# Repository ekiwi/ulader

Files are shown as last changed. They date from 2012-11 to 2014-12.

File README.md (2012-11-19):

# uLader #

This project aims at creating a backup battery powered bike
lighting system.
It borrows from the great work done by the developers of the
Forumslader and acknowledges this by incorporation
Lader (german for charger) into its name.
The u stands for the micro controller used in this design,
the use of which is going to add a lot more flexibility.

## Component Overview ##

The uLader system consists of these components:
* Main Board: atmega88 uC, ac to dc circuit, charging circuit, 
control switches
* Tail Light: red low power led (dimmable), photo transistor
* Front Light: attiny uC, white low power DLR (dimmabel), white 3W led 
(dimmable), photo transistor
* 2x Rotation Sensor: front and back

## Optional/Future Features ##
* White LED(s) underneath the saddle that can be turned on to find your locks
keyhole
* Pressure Sensor underneath/in the saddle to detect if someone is riding the
bike
* Turn signals on front and back

### Main Board ###

The main board contains the circuit that converts the power from the bike
dynamo, which acts approximately like an AC current source, to about 12V DC.
This circuit is heavily based on the awesome work done by the people behind
the [Forumslader project](forumslader.de).
This circuit is also responsible for charging the LiFePo4 accumulators used.
Check out [forumnslader.de]
(http://www.forumslader.de/Akkus-fuer-12V-Lader.189.0.html) if you want to use
different batteries.

The micro controller part of the Main Board features an atmega88. It was choosen,
because of its ease of use, its low power consumption and because if the number
of pins available.
The atmega is used for the following:
* power mangagement
    * check charging status
    * (indicate status??)
    * cut of power to all devices when battery cells run low
* lighting control
    * measure light intensity
    * measure speed
    * control which lights need to be on and how bright they need to be
    * in auto mode decide when to turn on which lights and auto dim

### Tail Light ####

The Tail Light needs to ensure visibility during the night (and day) from the 
back as well as from the side. In addition to that it must not blind other 
people.  
The CAT4201 led step down driver is used in combination with an OSRAM Top LED
in order to provide a low power solution for these requirements. The tail
light also includes a photo transistor for measuring the ambient light.  
It should be tested if visibility from the side of your bike can be enhanced
by adding one LED on each side.

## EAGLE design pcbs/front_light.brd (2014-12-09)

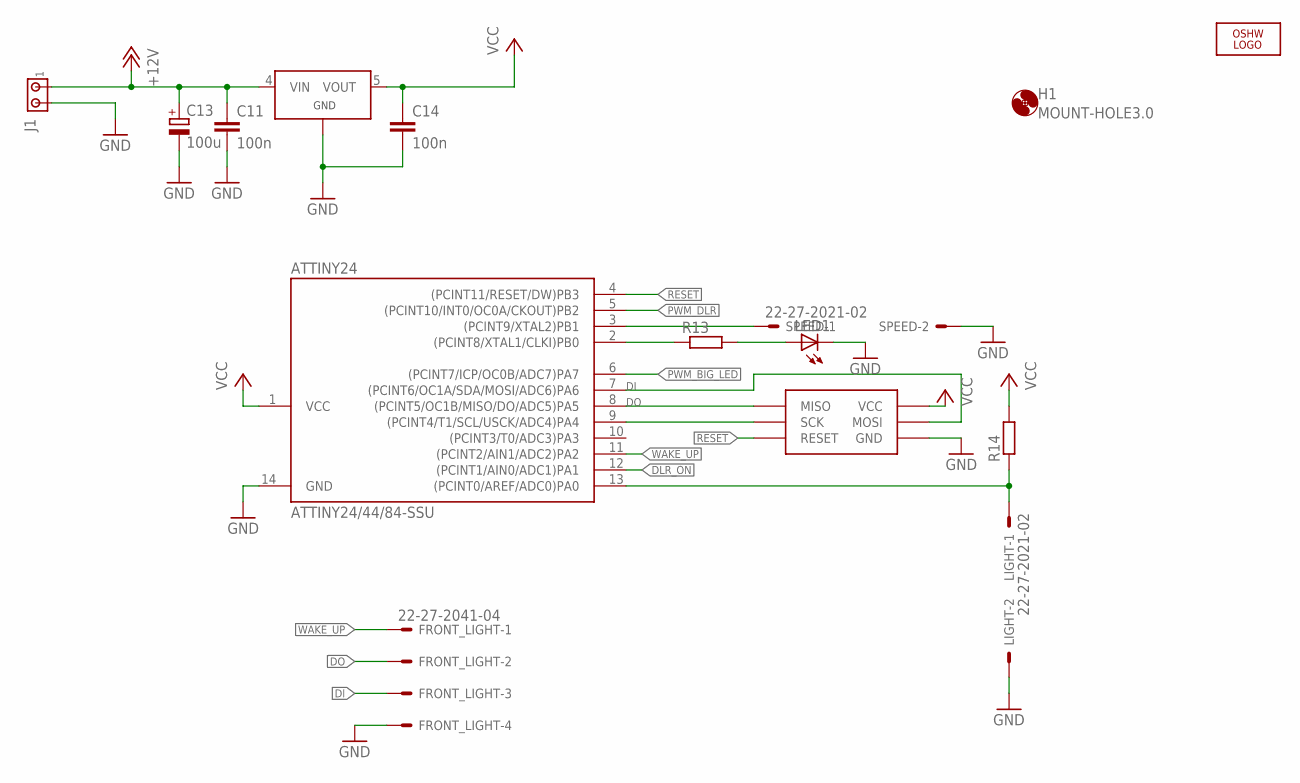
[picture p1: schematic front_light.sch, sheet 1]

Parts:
ATTINY24: ATTINY24/44/84-SSU; SOIC14
C11, C14: 100n; C0603
C13: 100u; PANASONIC_E
FRONT_LIGHT: 22-27-2041-04; 6410-04
H1: MOUNT-HOLE3.0; 3,0
J1: MTA02-156; 1X2MTA
LED1: LEDCHIPLED_0603; CHIPLED_0603
LIGHT: 22-27-2021-02; 6410-02
LOGO2: OSHW_LOGO_6MILX0150-NT; OSHW_6X150_NOTEXT
R13, R14: R-EU_R0603; R0603
SPEED: 22-27-2021-02; 6410-02
U$1: TPS71530; SOT23-DBV
U$2: ISP_SPECIALS; ISP_RM2_00_STRAIGHT

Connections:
+12V: C11.1, C13.+, J1.1, U$1.4 (VIN); also elsewhere on the board
DI: ATTINY24.7 ((PCINT6/OC1A/SDA/MOSI/ADC6)PA6), FRONT_LIGHT.3, U$2.MOSI
DLR_ON: ATTINY24.12 ((PCINT1/AIN0/ADC1)PA1); also elsewhere on the board
DO: ATTINY24.8 ((PCINT5/OC1B/MISO/DO/ADC5)PA5), FRONT_LIGHT.2, U$2.RESET (MISO)
GND: ATTINY24.14 (GND), C11.2, C13.-, C14.2, FRONT_LIGHT.4, J1.2, LED1.C, LIGHT.2, SPEED.2, U$1.2 (GND), U$2.VCC (GND); also elsewhere on the board
unnamed: ATTINY24.3 ((PCINT9/XTAL2)PB1), SPEED.1
unnamed: ATTINY24.9 ((PCINT4/T1/SCL/USCK/ADC4)PA4), U$2.SCK
unnamed: ATTINY24.13 ((PCINT0/AREF/ADC0)PA0), LIGHT.1, R14.1
unnamed: ATTINY24.2 ((PCINT8/XTAL1/CLKI)PB0), R13.1
unnamed: LED1.A, R13.2
PWM_BIG_LED: ATTINY24.6 ((PCINT7/ICP/OC0B/ADC7)PA7); also elsewhere on the board
PWM_DLR: ATTINY24.5 ((PCINT10/INT0/OC0A/CKOUT)PB2); also elsewhere on the board
RESET: ATTINY24.4 ((PCINT11/RESET/DW)PB3), U$2.MISO (RESET)
VCC: ATTINY24.1 (VCC), C14.1, R14.2, U$1.5 (VOUT), U$2.GND (VCC)
WAKE_UP: ATTINY24.11 ((PCINT2/AIN1/ADC2)PA2), FRONT_LIGHT.1

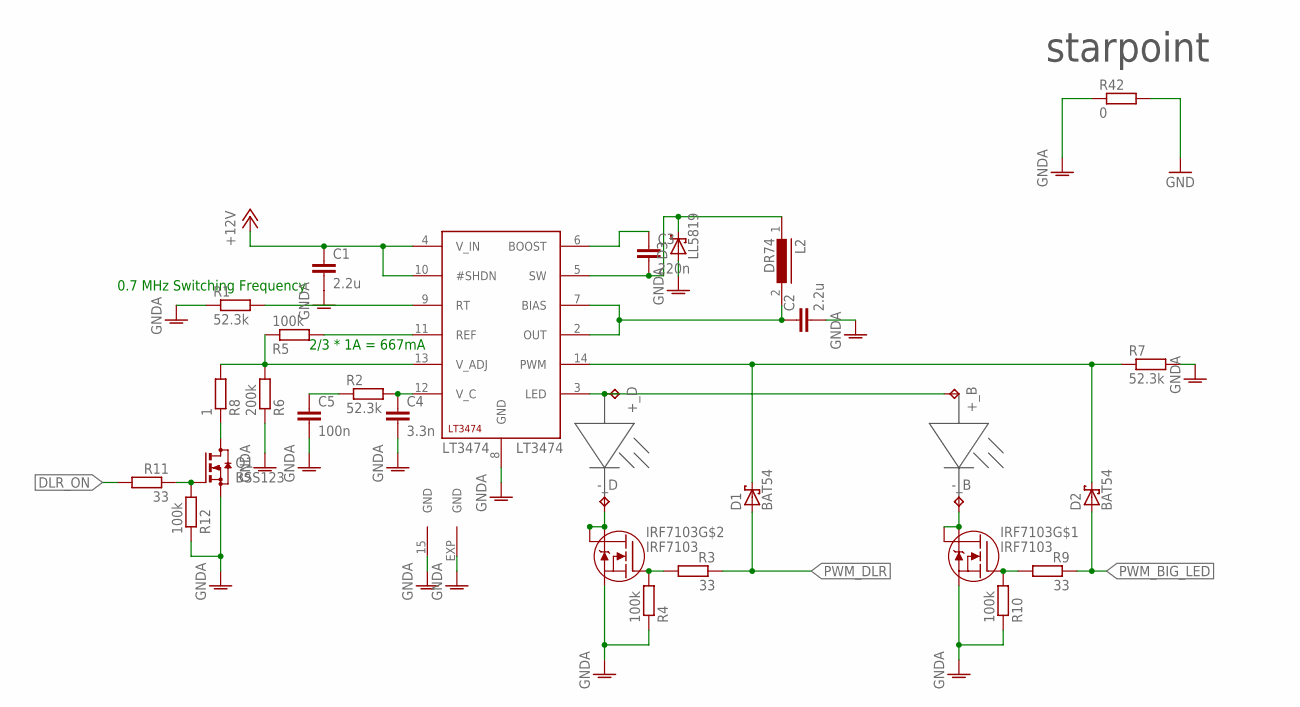
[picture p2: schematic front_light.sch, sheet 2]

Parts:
+_B: TPTP20SQ; TP20SQ
+_D: TPTP20SQ; TP20SQ
-_B: TPTP20SQ; TP20SQ
-_D: TPTP20SQ; TP20SQ
C1, C2: 2.2u; C0805
C3: 220n; C0603
C4: 3.3n; C0603
C5: 100n; C0603
D1, D2: BAT54; SOT23
D3: LL5819; MELF-MLL41
IRF7103: IRF7103; SO8-2
L2: DR74
LT3474: LT3474; TSSOP16_BA
Q1: BSS123; SOT23
R1, R2, R7: 52.3k; R0603
R3, R9, R11: 33; R0603
R4, R5, R10, R12: 100k; R0603
R6: 200k; R0603
R8: 1; R0603
R42: 0; R0603

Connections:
+12V: C1.1, LT3474.4 (V_IN), LT3474.10 (#SHDN); also elsewhere on the board
DLR_ON: R11.2; also elsewhere on the board
GND: R42.2; also elsewhere on the board
GNDA: C1.2, C2.2, C4.2, C5.2, D3.A, IRF7103.1 (S), IRF7103.3 (S), LT3474.8 (GND), LT3474.15 (GND), LT3474.EXP (GND), Q1.2 (S), R1.1, R4.1, R6.1, R7.2, R10.1, R12.1, R42.1
unnamed: C3.2, D3.C, L2.1, LT3474.5 (SW)
unnamed: C2.1, L2.2, LT3474.2 (OUT), LT3474.7 (BIAS)
unnamed: LT3474.11 (REF), R5.2
unnamed: LT3474.9 (RT), R1.2
unnamed: C3.1, LT3474.6 (BOOST)
unnamed: C4.1, LT3474.12 (V_C), R2.2
unnamed: C5.1, R2.1
unnamed: +_B.TP, +_D.TP, LT3474.3 (LED)
unnamed: -_D.TP, IRF7103.5 (D), IRF7103.6 (D)
unnamed: IRF7103.4 (G), R3.2, R4.2
unnamed: LT3474.13 (V_ADJ), R5.1, R6.2, R8.2
unnamed: Q1.3 (D), R8.1
unnamed: Q1.1 (G), R11.1, R12.2
unnamed: -_B.TP, IRF7103.7 (D), IRF7103.8 (D)
unnamed: IRF7103.2 (G), R9.2, R10.2
PWM: D1.3 (C), D2.3 (C), LT3474.14 (PWM), R7.1
PWM_BIG_LED: D2.1 (A), R9.1; also elsewhere on the board
PWM_DLR: D1.1 (A), R3.1; also elsewhere on the board

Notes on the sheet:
0.7 MHz Switching Frequency
2/3 * 1A = 667mA
starpoint

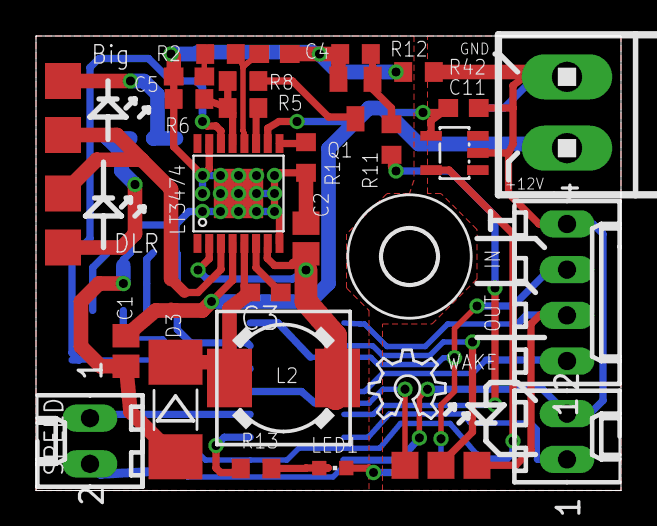
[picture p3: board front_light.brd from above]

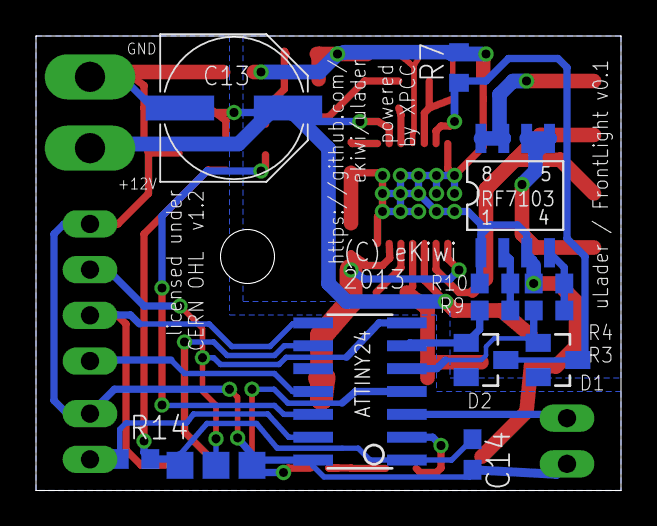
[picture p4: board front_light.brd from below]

Board: 2 copper layers, 32.5 x 25.2 mm, 44 parts (12 on the bottom side), 32 nets.

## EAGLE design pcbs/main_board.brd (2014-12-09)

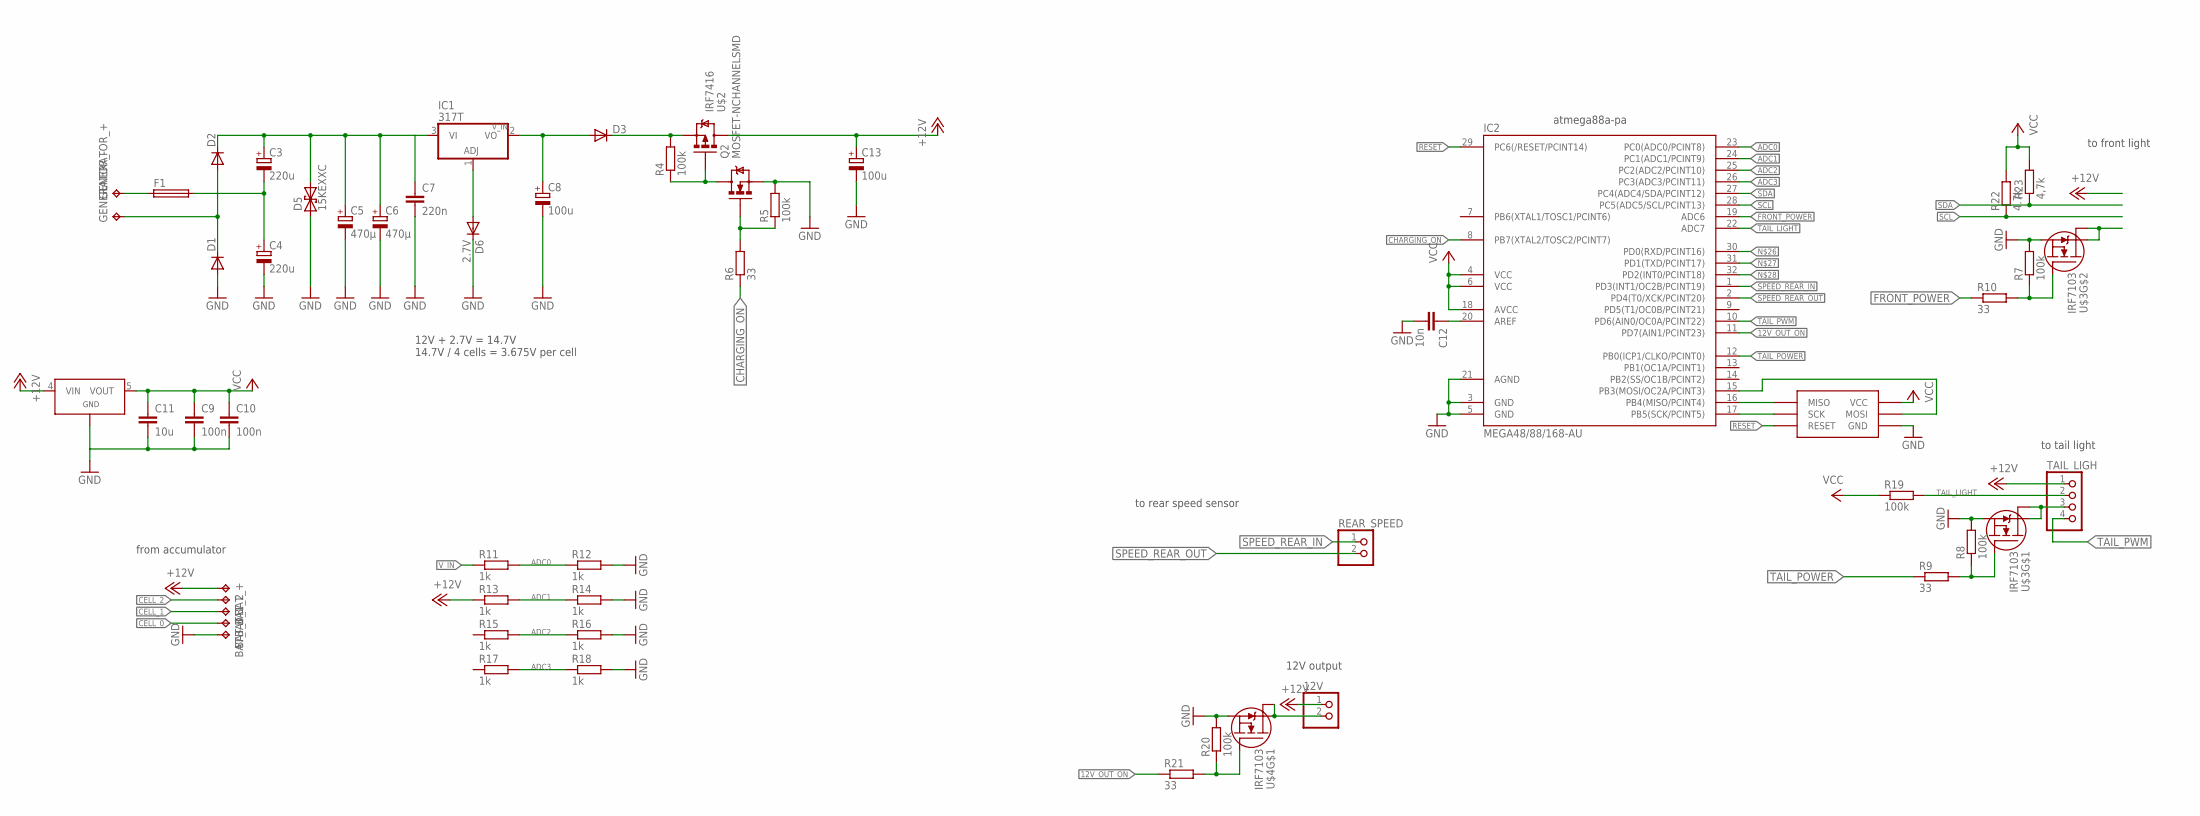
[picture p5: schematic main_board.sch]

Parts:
12V: PINHD-1X2; 1X02
BAT_0, BAT_1, BAT_2: TPTP18SQ; TP18SQ
BAT_+: TPTP18SQ; TP18SQ
BAT_-: TPTP18SQ; TP18SQ
C3, C4: 220u; PANASONIC_F
C5, C6: 470µ; 153CLV-1014
C7: 220n; C0805
C8, C13: 100u; PANASONIC_E
C9, C10: 100n; C0805
C11: 10u; C1206
C12: 10n; C0805
D1, D2, D3: DIODE-DO-214AC; DO-214AC
D5: 15KEXXC; CB429-17
D6: 2.7V; MINIMELF
F1: TE5
GENERATOR_+: TPTP18SQ; TP18SQ
GENERATOR_-: TPTP18SQ; TP18SQ
IC1: 317T; TO220H
IC2: MEGA48/88/168-AU; TQFP32-08
Q2: MOSFET-NCHANNELSMD; SOT23-3
R4, R5, R7, R8, R19, R20: 100k; R0603
R6, R9, R10, R21: 33; R0603
R11, R12, R13, R14, R15, R16, R17, R18: 1k; R0603
R22: 4.7k; R0603
R23: 4,7k; R0603
REAR_SPEED: PINHD-1X2; 1X02
TAIL_LIGH: PINHD-1X4; 1X04
U$1: TPS71530; SOT23-DBV
U$2: IRF7416; SO8-2
U$3, U$4: IRF7103; SO8-2
U$5: ISP_SPECIALS; ISP_RM2_00_STRAIGHT

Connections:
12V_OUT_ON: IC2.11 (PD7(AIN1/PCINT23)), R21.1
+12V: 12V.1, BAT_+.TP, C13.+, R13.1, TAIL_LIGH.1, U$1.4 (VIN), U$2.5 (D1), U$2.6 (D1), U$2.7 (D1), U$2.8 (D1)
ADC0: IC2.23 (PC0(ADC0/PCINT8)), R11.2, R12.1
ADC1: IC2.24 (PC1(ADC1/PCINT9)), R13.2, R14.1
ADC2: IC2.25 (PC2(ADC2/PCINT10)), R15.2, R16.1
ADC3: IC2.26 (PC3(ADC3/PCINT11)), R17.2, R18.1
CELL_0: BAT_0.TP
CELL_1: BAT_1.TP
CELL_2: BAT_2.TP
CHARGING_ON: IC2.8 (PB7(XTAL2/TOSC2/PCINT7)), R6.1
FRONT_POWER: IC2.19 (ADC6), R10.1
GND: BAT_-.TP, C4.-, C5.-, C6.-, C7.2, C8.-, C9.2, C10.2, C11.2, C12.2, C13.-, D1.A, D5.A (1), D6.C, IC2.3 (GND), IC2.5 (GND), IC2.21 (AGND), Q2.2 (S), R5.2, R7.2, R8.2, R12.2, R14.2, R16.2, R18.2, R20.2, U$1.2 (GND), U$3.1 (S), U$3.3 (S), U$4.1 (S), U$5.VCC (GND)
unnamed: D3.C, R4.2, U$2.1 (S1), U$2.2 (S1), U$2.3 (S1)
unnamed: C12.1, IC2.20 (AREF)
unnamed: D1.C, D2.A, GENERATOR_-.TP
unnamed: 12V.2, U$4.7 (D), U$4.8 (D)
unnamed: IC2.17 (PB5(SCK/PCINT5)), U$5.SCK
unnamed: C3.-, C4.+, F1.2
unnamed: F1.1, GENERATOR_+.TP
unnamed: D6.A, IC1.1 (ADJ)
unnamed: IC2.16 (PB4(MISO/PCINT4)), U$5.RESET (MISO)
unnamed: U$3.5 (D), U$3.6 (D)
unnamed: Q2.3 (D), R4.1, U$2.4 (G)
unnamed: Q2.1 (G), R5.1, R6.2
unnamed: TAIL_LIGH.3, U$3.7 (D), U$3.8 (D)
unnamed: R7.1, R10.2, U$3.4 (G)
unnamed: R8.1, R9.2, U$3.2 (G)
unnamed: IC2.15 (PB3(MOSI/OC2A/PCINT3)), U$5.MOSI
unnamed: R20.1, R21.2, U$4.2 (G)
unnamed: C8.+, D3.A, IC1.2 (VO)
RESET: IC2.29 (PC6(/RESET/PCINT14)), U$5.MISO (RESET)
SCL: IC2.28 (PC5(ADC5/SCL/PCINT13)), R22.1
SDA: IC2.27 (PC4(ADC4/SDA/PCINT12)), R23.1
SPEED_REAR_IN: IC2.1 (PD3(INT1/OC2B/PCINT19)), REAR_SPEED.1
SPEED_REAR_OUT: IC2.2 (PD4(T0/XCK/PCINT20)), REAR_SPEED.2
TAIL_LIGHT: IC2.22 (ADC7), R19.2, TAIL_LIGH.2
TAIL_POWER: IC2.12 (PB0(ICP1/CLKO/PCINT0)), R9.1
TAIL_PWM: IC2.10 (PD6(AIN0/OC0A/PCINT22)), TAIL_LIGH.4
VCC: C9.1, C10.1, C11.1, IC2.4 (VCC), IC2.6 (VCC), IC2.18 (AVCC), R19.1, R22.2, R23.2, U$1.5 (VOUT), U$5.GND (VCC)
V_IN: C3.+, C5.+, C6.+, C7.1, D2.C, D5.C (2), IC1.3 (VI), R11.1

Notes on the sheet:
atmega88a-pa
to front light
to tail light
from accumulator
to rear speed sensor
12V output
12V + 2.7V = 14.7V 14.7V / 4 cells = 3.675V per cell

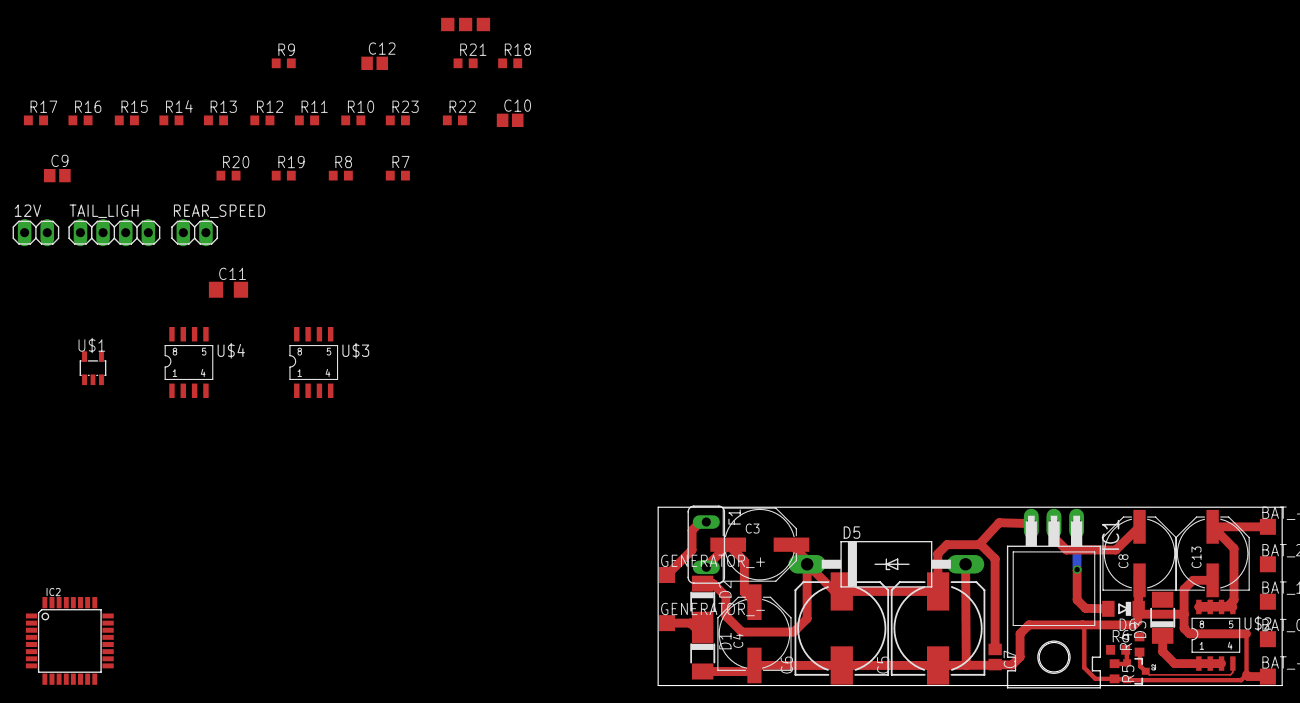
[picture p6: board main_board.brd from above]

Board: 2 copper layers, 70.0 x 20.0 mm, 55 parts (0 on the bottom side), 37 nets.

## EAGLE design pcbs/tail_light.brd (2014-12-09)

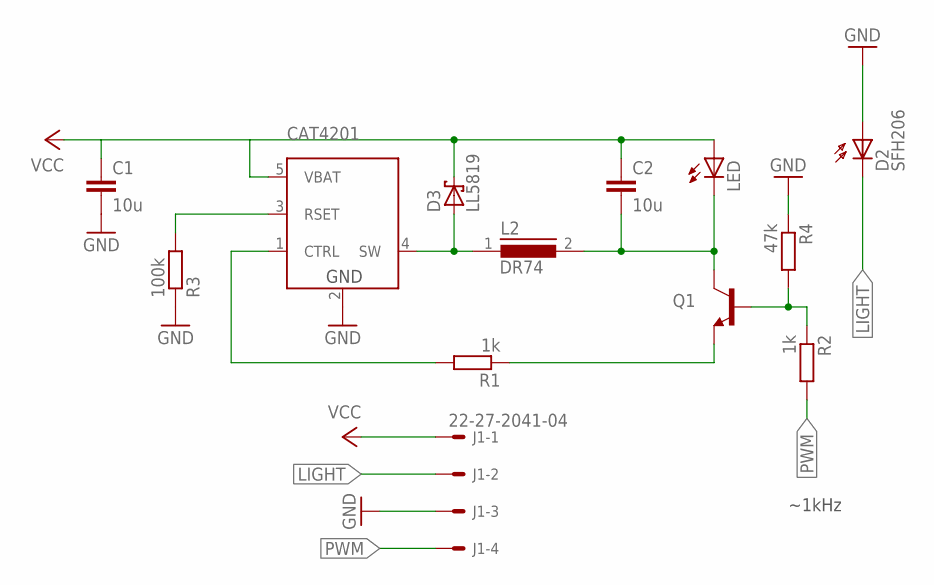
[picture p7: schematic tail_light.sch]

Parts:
C1, C2: 10u; C0805
CAT4201: CAT4201TF; SOT23-DBV
D2: SFH206
D3: LL5819; MELF-MLL41
J1: 22-27-2041-04; 6410-04
L2: DR74
LED: LEDMINI-TOP; OSRAM-MINI-TOP-LED
Q1: TRANSISTOR_NPNSOT23-3; SOT23-3
R1, R2: 1k; R1206
R3: 100k; R1206
R4: 47k; R1206

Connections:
GND: C1.2, CAT4201.2 (GND), D2.A, J1.3, R3.1, R4.1
LED_C: C2.2, L2.2, LED.C, Q1.3 (C)
LIGHT: D2.K (C), J1.2
unnamed: CAT4201.1 (CTRL), R1.2
unnamed: Q1.1 (B), R2.1, R4.2
unnamed: Q1.2 (E), R1.1
unnamed: CAT4201.4 (SW), D3.A, L2.1
unnamed: CAT4201.3 (RSET), R3.2
PWM: J1.4, R2.2
VCC: C1.1, C2.1, CAT4201.5 (VBAT), D3.C, J1.1, LED.A

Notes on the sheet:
~1kHz

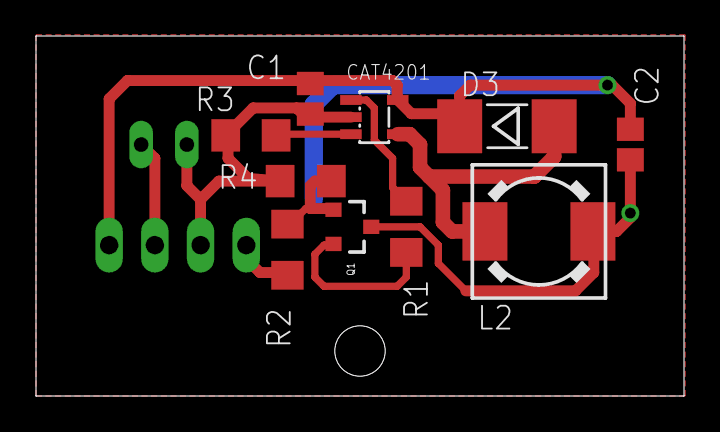
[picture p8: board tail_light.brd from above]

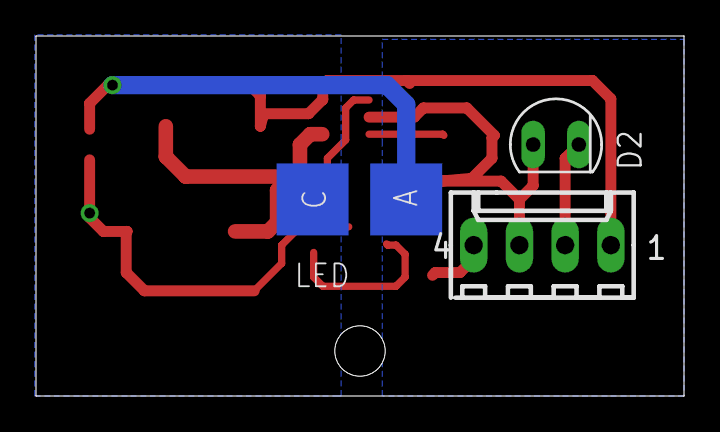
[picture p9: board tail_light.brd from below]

Board: 2 copper layers, 36.0 x 20.0 mm, 13 parts (3 on the bottom side), 10 nets.

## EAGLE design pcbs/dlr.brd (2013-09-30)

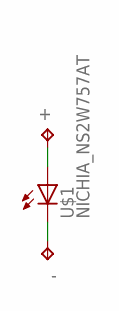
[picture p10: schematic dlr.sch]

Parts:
+: TPTP20SQ; TP20SQ
-: TPTP20SQ; TP20SQ
U$1: NICHIA_NS2W757AT

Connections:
+: +.TP, U$1.ANODE (A)
-: -.TP, U$1.CATHODE (C)

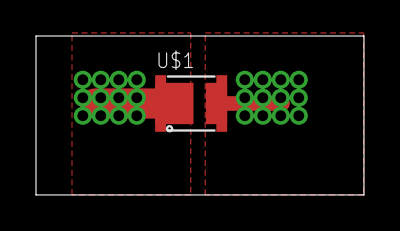
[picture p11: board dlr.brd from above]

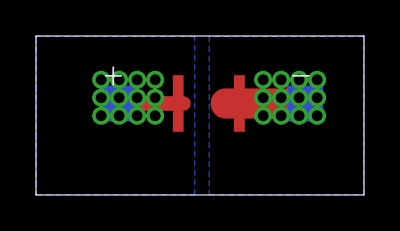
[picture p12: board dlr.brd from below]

Board: 2 copper layers, 18.2 x 8.8 mm, 3 parts (2 on the bottom side), 2 nets.

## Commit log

2012-10-03 Added initial gitignore file for eagle pcbs
2012-10-03 Added initial pcbs
    [ac_dc.brd, ac_dc.sch, front_light.brd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]
2012-10-03 AC/DC: Added atmega88 and power supply.
    [ac_dc.brd, ac_dc.sch]
2012-10-05 Readme: Added component overview and main board info.
2012-10-05 Readme: added main board and tail light description.
2012-10-07 Main Board: Added battery connector + mosfet switch
    [ac_dc.brd, ac_dc.sch]
2012-10-07 Renamed ac_dc.* to main_board.*
    [main_board.brd, main_board.sch]
2012-10-07 Main Board: Added connections to front and to tail light.
    [main_board.brd, main_board.sch]
2012-10-07 Main Board: Expanded Board to 120 x 20 mm
    [main_board.brd]
2012-10-08 Main Board: Changed fuse and corrected wrong connection.
    [main_board.brd, main_board.sch]
2012-10-08 Main Board: Added resistor dividers for voltage measurements.
    [main_board.brd, main_board.sch]
2012-10-08 Main Board: Added switchable 12V output.
    [main_board.brd, main_board.sch]
2012-10-08 Main Board: added i2c pullups.
    [main_board.brd, main_board.sch]
2012-10-08 Main Board: Changed battery connection.
    It does not make sense to disconnect the battery from the uC....
    Instead it makes sense to disconnect the charging/input circuit
    when the battery is full and disconnect the peripherals when it is
    getting empty.
    [main_board.brd, main_board.sch]
2012-10-12 Main Board: Added back i2c
    [main_board.brd, main_board.sch]
2012-10-12 Main Board: Started layouting control part
    [main_board.brd, main_board.sch]
2013-09-29 Main: fixed inconsitency between sch and brd
    [main_board.brd]
2013-09-29 Front light: use attiny and LT3474
    [front_light.brd, front_light.sch]
2013-09-29 ForntLight: improved silkscreen
    [front_light.brd, front_light.sch]
2013-09-29 FrontLight: solved some DRC errors
    If the .dru file from OSH Park is used
    and clearance od same signal smd, pad and via
    is set to 0, we do not get any DRC errors.
    [front_light.brd]
2013-09-30 FrontLight: use only one LT3474
    Since the DLR and the big led will never be used
    together they can be driven by a single
    led constant current switching IC.
    [front_light.brd, front_light.sch]
2013-09-30 DLR: add preliminary breakoutboard
    [dlr.brd, dlr.sch]
2013-10-20 Front Light: change via drill size to 0.5mm
    [front_light.brd]
2014-12-09 Pcbs: latest changes
    [front_light.brd, front_light.sch, main_board.brd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]

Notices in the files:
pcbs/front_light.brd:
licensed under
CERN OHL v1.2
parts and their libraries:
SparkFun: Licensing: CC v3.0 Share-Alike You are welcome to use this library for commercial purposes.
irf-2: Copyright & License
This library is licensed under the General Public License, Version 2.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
